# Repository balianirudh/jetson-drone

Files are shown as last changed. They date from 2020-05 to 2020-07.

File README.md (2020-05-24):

# Jetson Drone

I have built two drones with the help of the Cooperative Distributions Systems Lab at the University of Cincinnati. I started working there in the fall of 2018 and have focused on learning different control systems applicable to drones. The first drone I worked on was very rudimentary. It used an Arduino Uno as the main processor and an IMU sensor to monitor the orientation of the drone.

Upon diving deeper into computer vision and more complex control systems, I decided to make a second drone, the Jetson Drone, that is better suited for high-level autonomy. The major improvement compared to the first drone is the integration of the NVIDIA Jetson TX2 and the use of a camera to give the drone hardware that is better suited for autonomy.

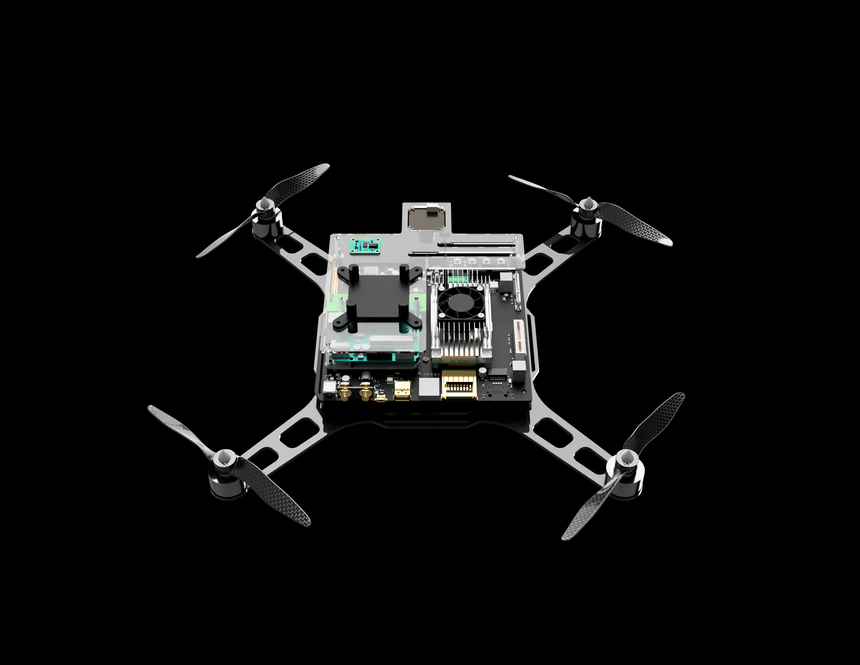
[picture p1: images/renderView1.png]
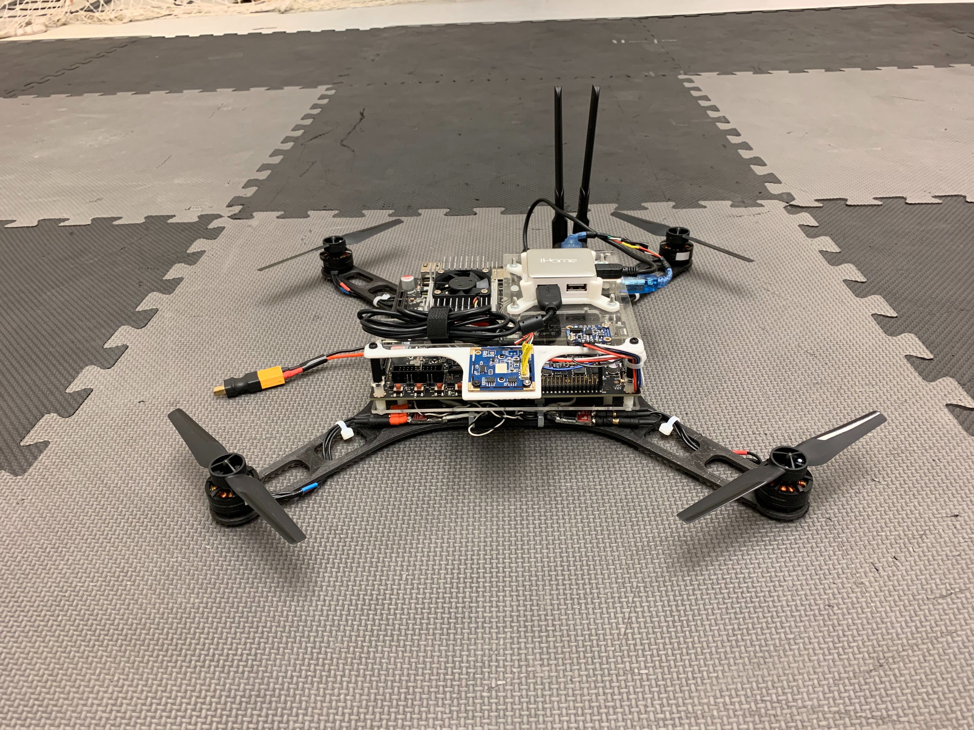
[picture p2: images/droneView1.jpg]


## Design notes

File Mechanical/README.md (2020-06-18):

# Mechancial System

## Frame

The first drone I designed featured laser cut acrylic arms and a top plate that were connected to the power distribtution board by 3D printed brackets. Although this was a sturdy frame and naturally stable due to its weight, it was too heavy for the motor and propeller system I was using. This gave the drone a very short flight time.

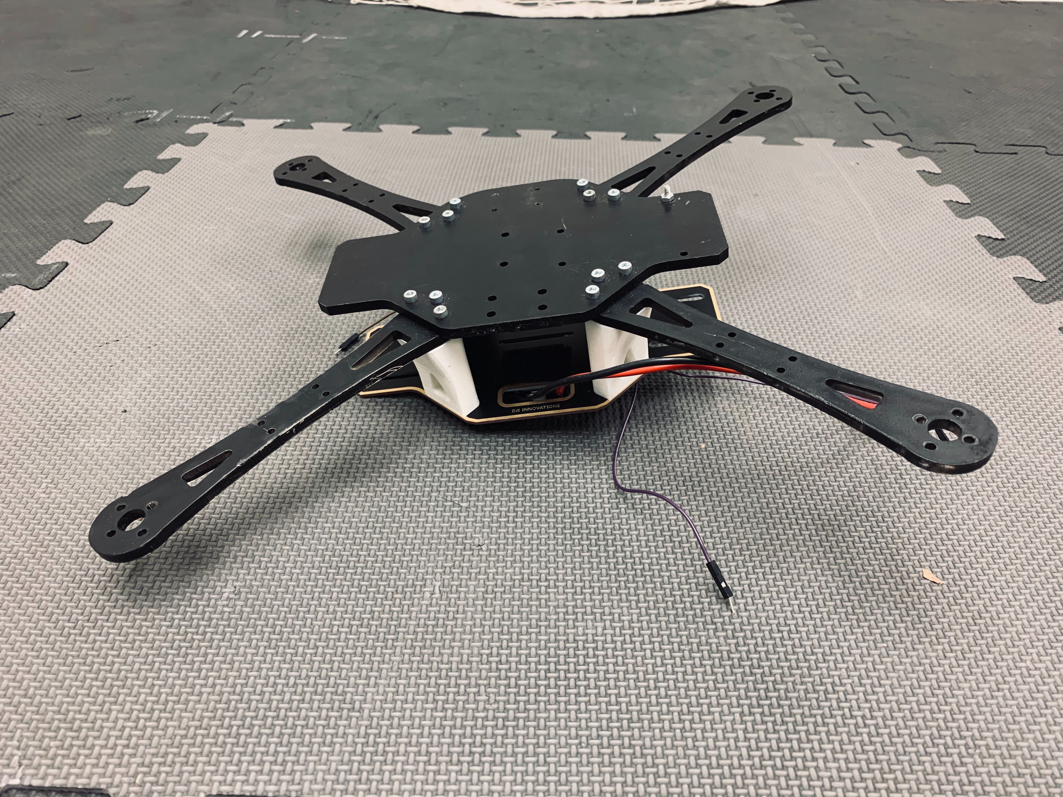
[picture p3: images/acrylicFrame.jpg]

<p align="center">Acrylic frame that was too heavy for prolonged flight times</p>

For the Jetson Drone, I kept in mind speed, agility, and ease of use when designing the frame. Alogn with this, I designed the frame specifically to house the NVIDIA Jetson TX2 carrier board as it has a fairly large footprint compared to most flight controllers used in drones.

The keep the weight low, I decided to 3D print the entire frame. I initially planned to use thinner laser cut acrylic parts but after testing, the thin arcylic arms were too flexible. The frame is made out of two pieces that are held together by a bracket on each side and the electronics mounting structure. However, standard PLA plastic was too flexible even with a high infill. To increase rigidity, I printed the frame out of a chopped carbon fiber and PLA blend. This provides the rigidity necessary in the drone arms while keeping the overall weight of the frame relatively low. 

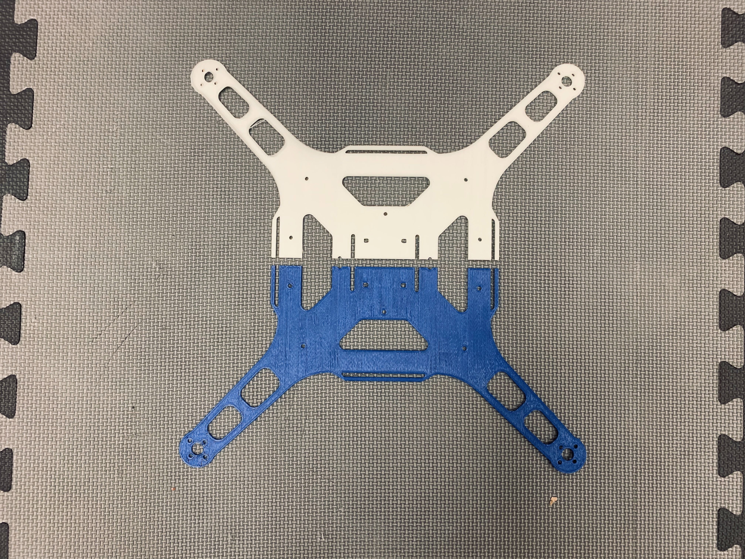
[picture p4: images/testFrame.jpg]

<p align="center">Test 3D print of frame using standard PLA (left), final drone assembly with chopped carbon fiber PLA frame (right)</p>

## Propulsion

The propulsion system of a drone is made up of its motor, electronic speed controller (ESC), and propeller. The combination of the three dictate the total thrust of the drone which impacts the drones overall agility. For the Jetson Drone, I chose to use the DJI Snail Propulstion system. This propulsion system was designed for racing drones meaning its lightweight, and depending on the propeller, has a high max thrust (2800g-5200g).

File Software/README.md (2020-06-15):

# Software

The Jetson TX2 onboard the drone runs Ubuntu 16.04 LTS as the operating system. This gives a tremendous amount of flexibility in regard to how programs can be run on the machine. To fly, the drone is running several different programs that communicate with each other using a publisher-subscriber model. This is done through the robot operating system (ROS) framework to make it a seamless process.

"flowchart of publisher-subscriber model here. refer to portfolio"

## Mobility Control

There are two main controllers that have been implemented on the Jetson drone. The first is a nested PID controller for attitude control. Raw IMU data is processed through a Kalman filter to reduce noise from the IMU. This data is then used by the PID controller to stabilize the drone for any desired orientation.

Rather than using a PID controller for the line following aspect of the drone, I decided to implement an LQR controller. The LQR controller is responisble for calculating each motor's angular velocity to follow a given path. This controller was used because of how it is based on the state-space representation of the system. Unlike other controller, LQR taes into account the dynamics of the drone which is advantageous when trying to move in a specific way.

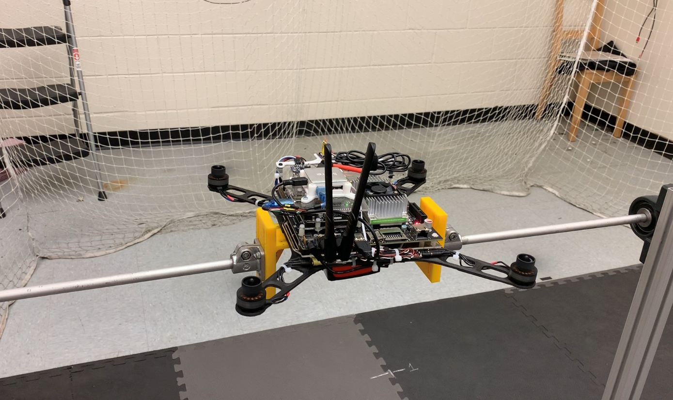
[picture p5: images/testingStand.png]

<p align="center"> Drone on test stand for stability tuning </p>

## Vision System

There are two cameras onboard the Jetson drone; however, currently, only one is being used. The camera that is being used is the downward-facing USB camera. This camera is responsible for taking a live recording of what is below the drone. The video is then  analyzed using OpenCV to determine where the desired path is.

"add flowchart of lane detection"  "add picture of lane detection in action"

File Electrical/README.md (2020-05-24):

# Electrical System

## Flight Controller

The drone carries an NVIDIA Jetson TX2 onboard. This is used as the main flight controller of the drone. The Jetson is capable of doing the necessary computation for video processing and the control system of the drone. Its high computing power made it perfect for the task of creating an autonomous drone and implementing an LQR controller.

Alongside the Jetson, an Arduino Uno is responsible for communicating the motor PWM signals to each ESC. After going through several calculations, the Jetson sends the respective PWM signal of each motor to the Arduino to set the speed of each motor.

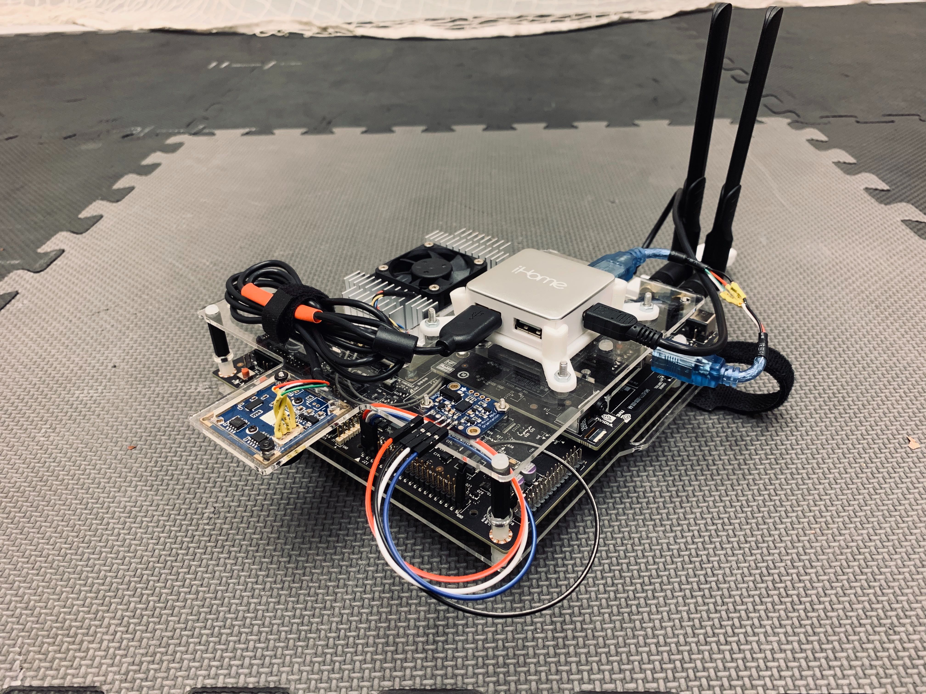
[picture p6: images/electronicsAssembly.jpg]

<p align="center"> Electronics Assembly </p>

## Sensors

There are 3 main sensors on the drone that give it the ability to do what it can do. A BNO055 IMU is connected to the Jeston's GPIO pins. This is necessary to read the current pitch, roll, and yaw angles to make adjustments to maintain a specific orientation. Along with this, 2 cameras are onboard. The main camera is a downward facing USB camera. This camera is meant to identify the path of the desired trajectory for the drone. Using the identified path and the current trajectory of the drone, I am able to calculate the error angle. This angle is used by the LQR controller to calculate the new angular velocities of each motor. 

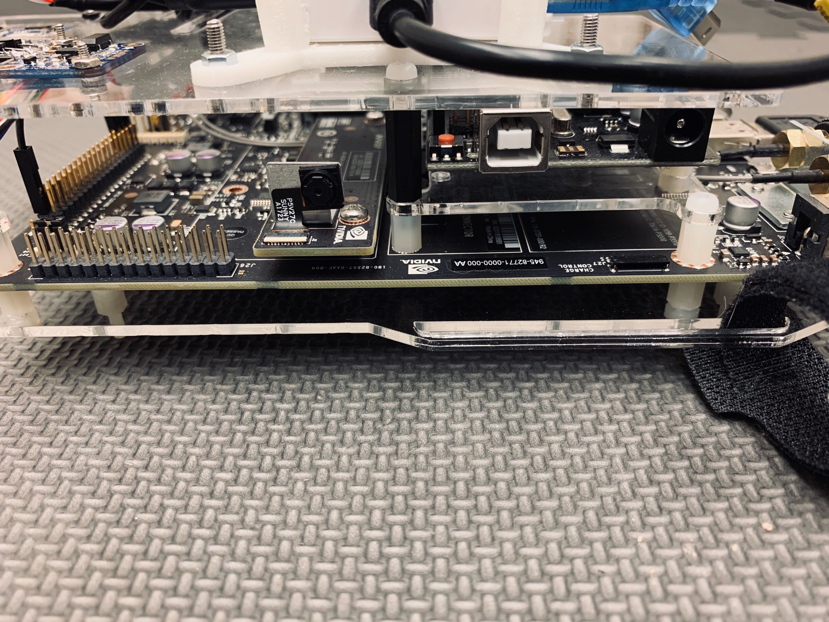
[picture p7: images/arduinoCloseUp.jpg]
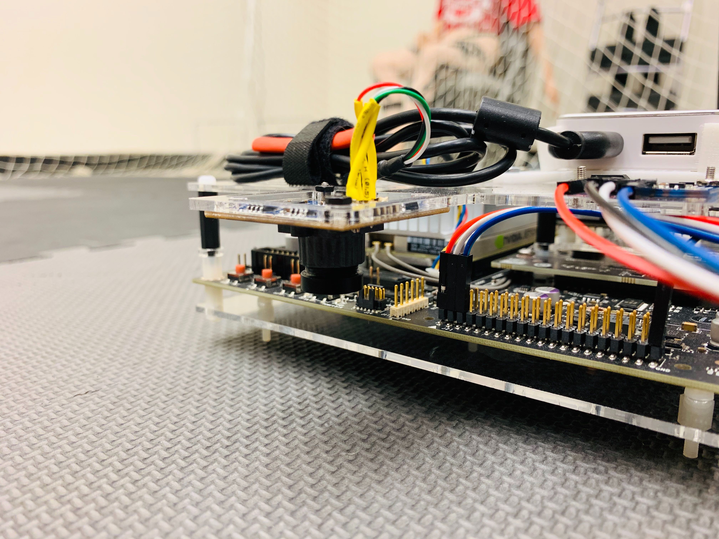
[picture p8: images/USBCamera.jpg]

<p align="center"> Jetson's onboard camera and mounted Arduino (left), Downward facing USB camera for line following (right) </p>

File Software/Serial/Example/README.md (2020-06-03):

# Serial Communication with Arduino LED

*Current code only works on Windows. In Linux, the data is sending to the Arduino and the Arduino is receiving it but I don't see the correct behavior from the LED. I believe the problem is that I need to configure the path of the Arduino so the Arduino recieved the correct data. Looking into how I can solve this issue.*

Serial communication is vital to the function of the drone because without it the drone would not receive motor commands. I am sure there is a way to use the GPIO pins of the Jetson to send PWM signals to the motor controllers, however, the Arduino platform makes this task straightforward. 

The purpose of this example to is demonstrate how the serial communication between the Jetson TX2 and Arduino Uno work on the drone. With this example, there is no need to calculate specific motor values or have the full ROS package of this project set up. Instead it uses the Arduino's onboard LED to demonstrate how data is being sent from a C++ program to the Arduino.

Note that even though the C++ program only sends data to the Arduino once, the Arduino's onboard LED continously blinks using data that was only sent once. This is because the variable receivedInts (in Arduino program) is never written over with new data and the function that blinks the LED is in a loop.

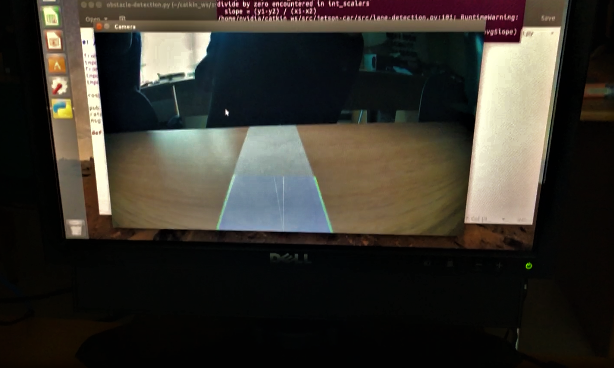
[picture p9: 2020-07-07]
images/pathDetectionExample.png

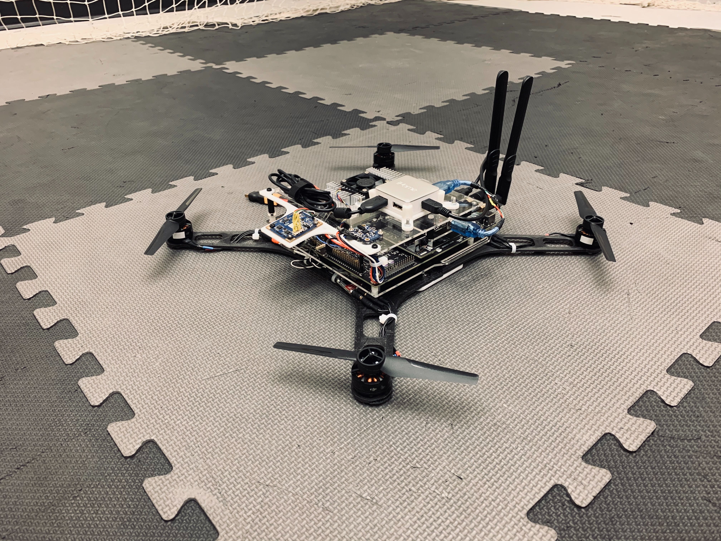
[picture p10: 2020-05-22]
images/droneView3.jpg

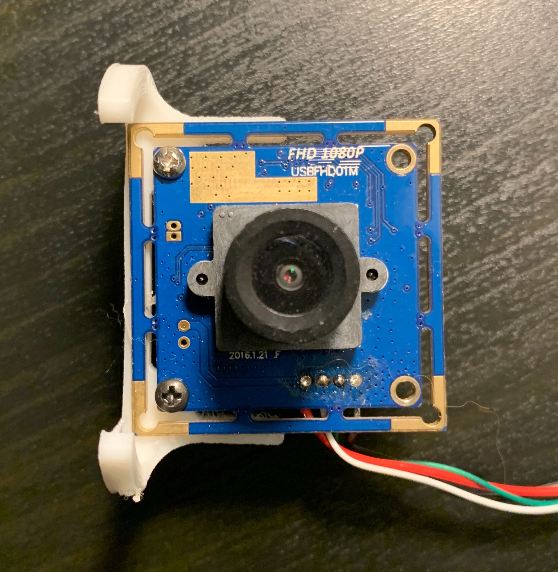
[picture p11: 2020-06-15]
images/USBCamera2.jpg

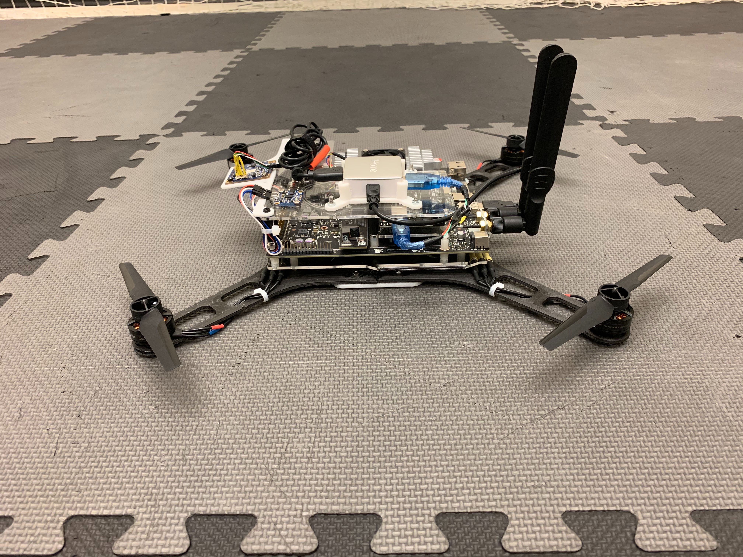
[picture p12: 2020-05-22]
images/droneView2.jpg

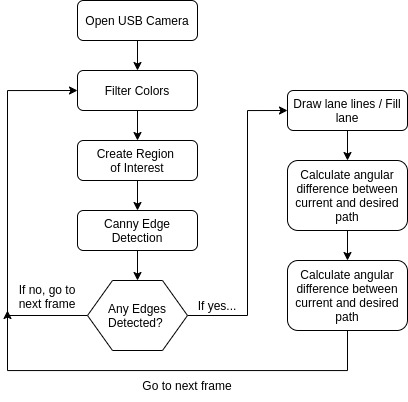
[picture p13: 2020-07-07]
images/videoProcessing1.jpg

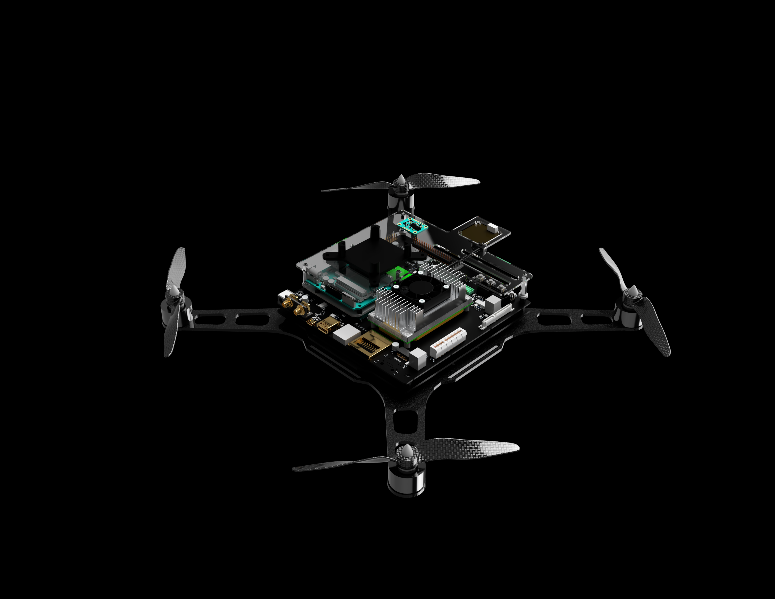
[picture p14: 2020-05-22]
images/renderView3.png

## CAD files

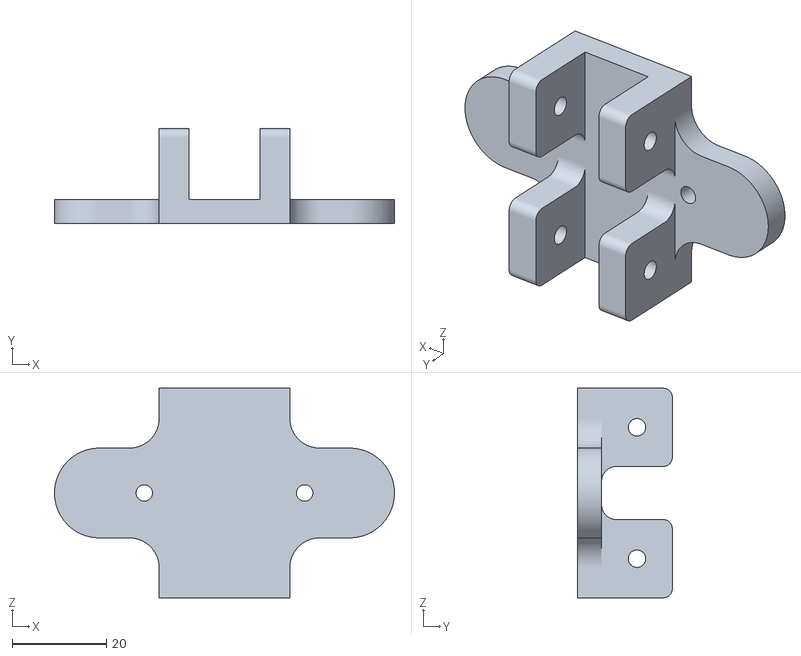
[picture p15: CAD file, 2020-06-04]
Mechanical/CAD/3DPrint/TestBracket.stl
72.1 x 20.1 x 44.4

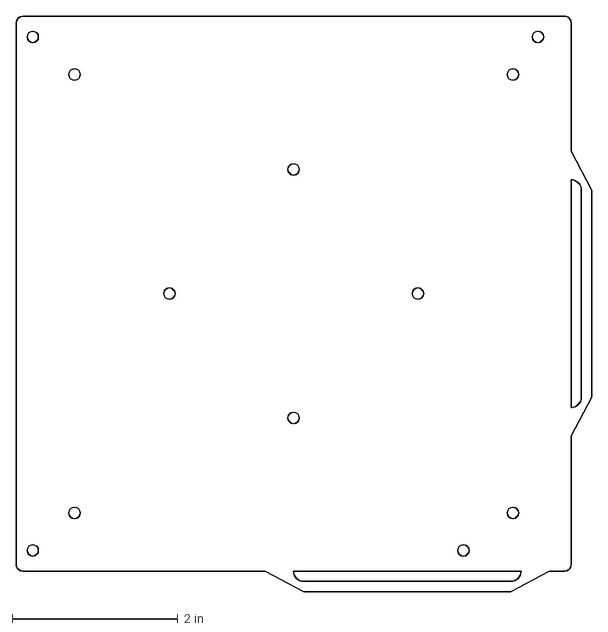
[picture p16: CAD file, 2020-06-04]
Mechanical/CAD/Lasercut/secondLayer.dxf
6.95 x 6.95 in

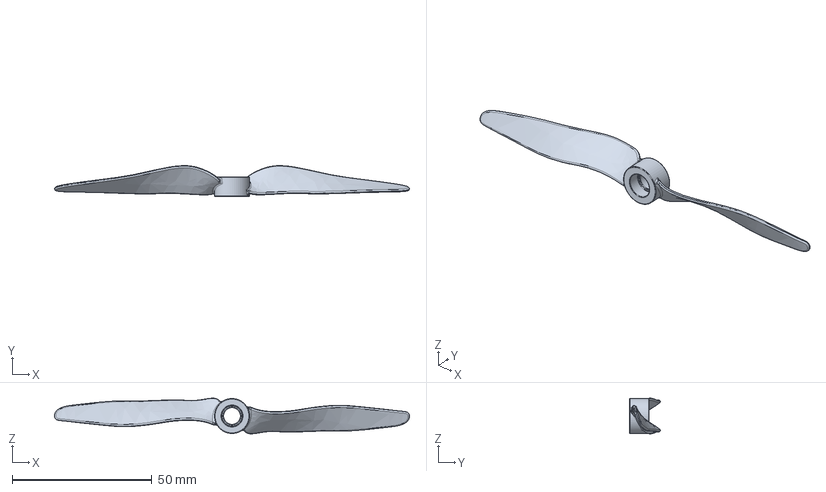
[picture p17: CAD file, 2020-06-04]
Mechanical/CAD/Propeller 5x5.step
127.0 x 11.0 x 12.8 mm

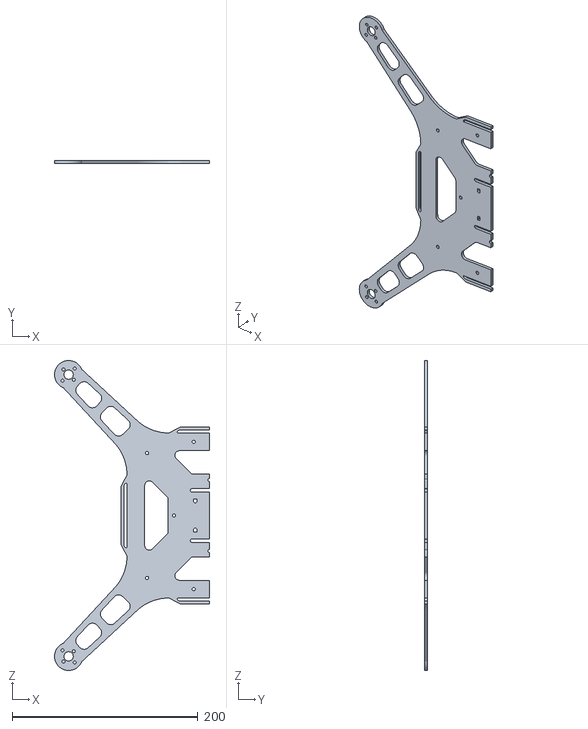
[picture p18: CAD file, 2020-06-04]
Mechanical/CAD/3DPrint/HalfFirstLayer.stl
167.0 x 3.17 x 334.0

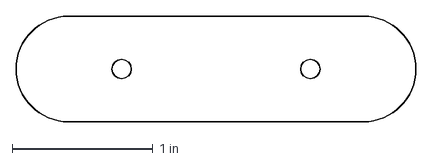
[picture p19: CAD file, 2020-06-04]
Mechanical/CAD/Lasercut/FrameBracket.dxf
2.84 x 0.75 in

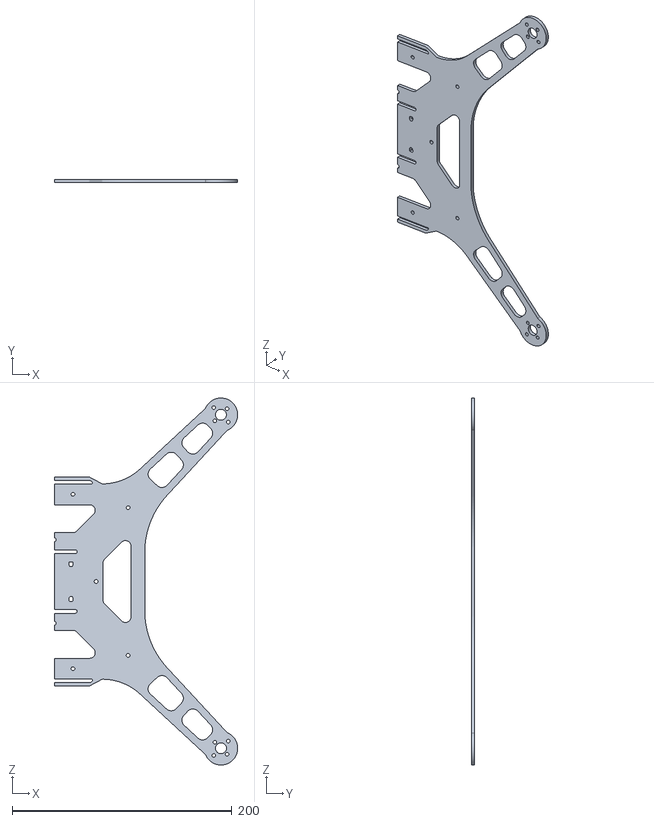
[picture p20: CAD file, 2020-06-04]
Mechanical/CAD/3DPrint/SecondHalf.stl
167.0 x 3.17 x 334.1

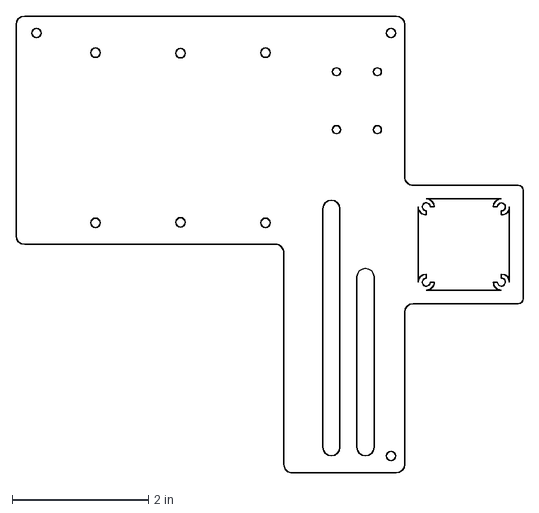
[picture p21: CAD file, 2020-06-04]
Mechanical/CAD/Lasercut/thirdLayer.dxf
7.43 x 6.70 in

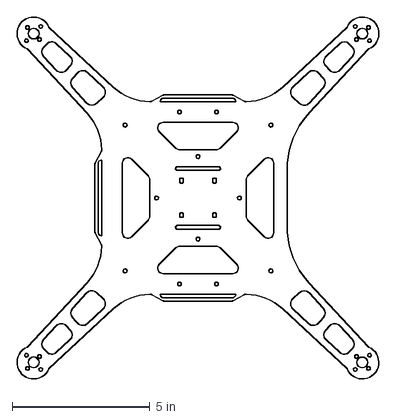
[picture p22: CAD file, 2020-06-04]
Mechanical/CAD/Lasercut/firstLayer.dxf
13.2 x 13.2 in

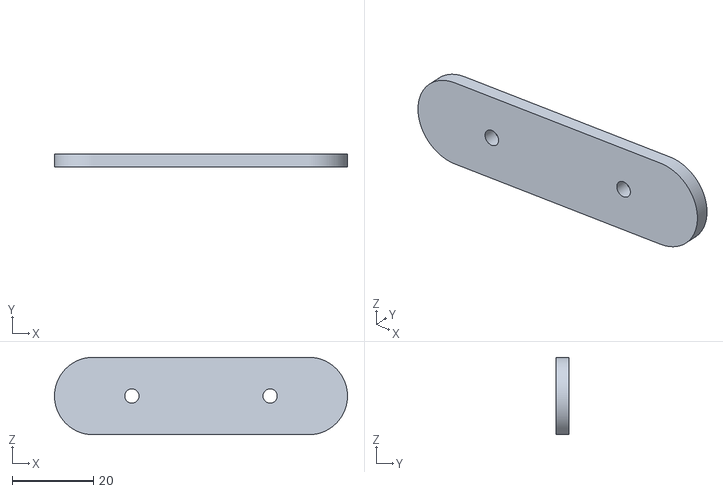
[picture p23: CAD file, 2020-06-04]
Mechanical/CAD/3DPrint/FrameBracket.stl
72.1 x 3.17 x 19.0

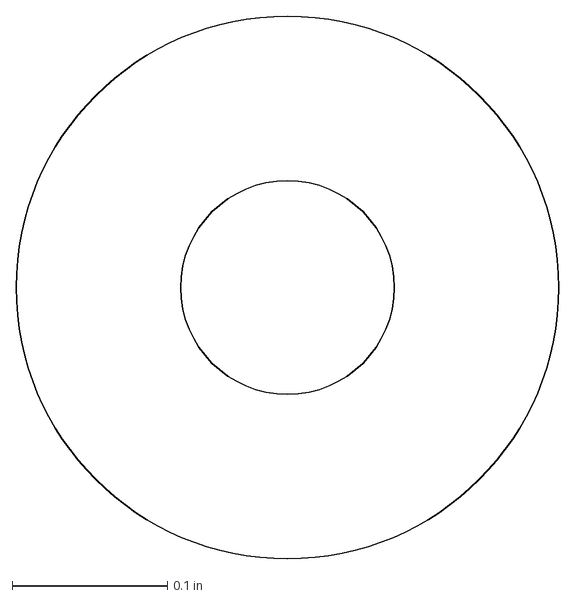
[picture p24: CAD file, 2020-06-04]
Mechanical/CAD/Lasercut/spacer.dxf
0.35 x 0.35 in

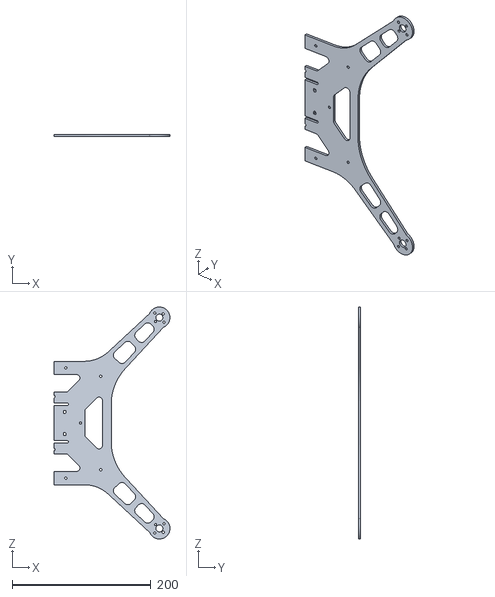
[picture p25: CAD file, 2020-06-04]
Mechanical/CAD/3DPrint/SecondHalf2.stl
167.0 x 3.17 x 334.1

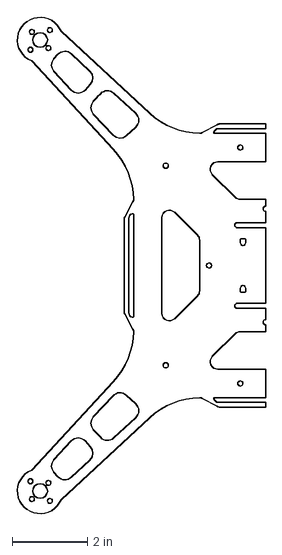
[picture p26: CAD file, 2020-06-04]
Mechanical/CAD/Lasercut/halfFirstLayer.dxf
6.60 x 13.2 in

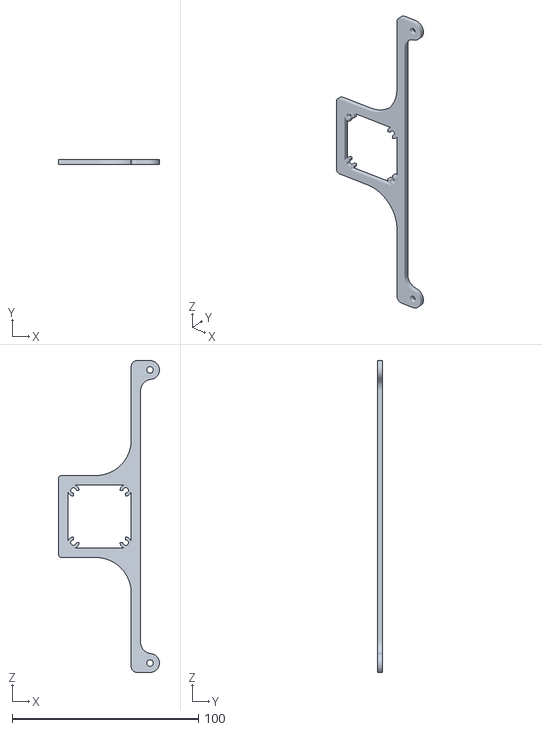
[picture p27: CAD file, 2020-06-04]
Mechanical/CAD/3DPrint/CameraBracket.stl
54.2 x 2.54 x 167.6

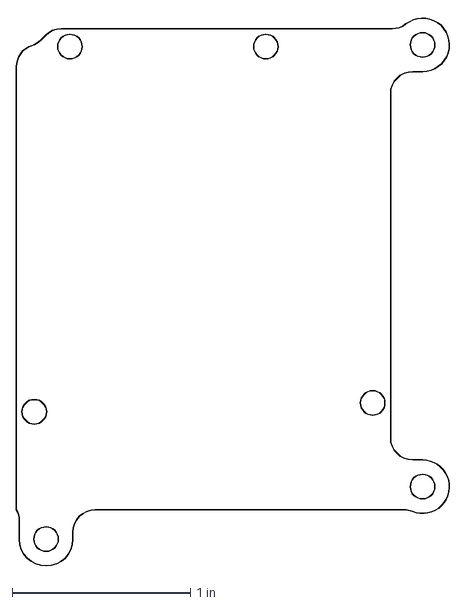
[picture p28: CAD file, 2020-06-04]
Mechanical/CAD/Lasercut/arduinoPlate.dxf
2.44 x 3.09 in

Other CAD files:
Mechanical/CAD/3DPrint/HalfFirstLayer2.stl
Mechanical/CAD/3DPrint/FirstLayer.stl
archives/FlameWheelFrame/FlameWheel_F450_Base_Bottom.SLDPRT
Mechanical/CAD/7x7 Propeller.ipt
Mechanical/CAD/Adafruit_BNO055_AP214.ipt
Mechanical/CAD/ArduinoPlate.ipt
Mechanical/CAD/CameraBracket.ipt
Mechanical/CAD/CameraMount.ipt
Mechanical/CAD/FirstLayer.ipt
Mechanical/CAD/FrameBracket.ipt
Mechanical/CAD/Hex Spacer MF M3 L20mm.ipt
Mechanical/CAD/Hex Spacer MF M3 L6mm.ipt
Mechanical/CAD/Hex Spacer MF M3 L8mm.ipt
Mechanical/CAD/LOW-LIGHT-HD-USB-CAMERA-R1.ipt
Mechanical/CAD/MotorMountingHub.ipt
Mechanical/CAD/Propeller 5x5.ipt
Mechanical/CAD/SecondLayer.ipt
Mechanical/CAD/SnailMotorModel.ipt
Mechanical/CAD/TestBracket.ipt
Mechanical/CAD/ThirdLayer.ipt
Mechanical/CAD/USBHubMount.ipt
Mechanical/CAD/spacer.ipt
archives/FlameWheelFrame/FlameWheel_F450.iam
archives/FlameWheelFrame/FlameWheel_F450_Base_Bottom.ipt
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

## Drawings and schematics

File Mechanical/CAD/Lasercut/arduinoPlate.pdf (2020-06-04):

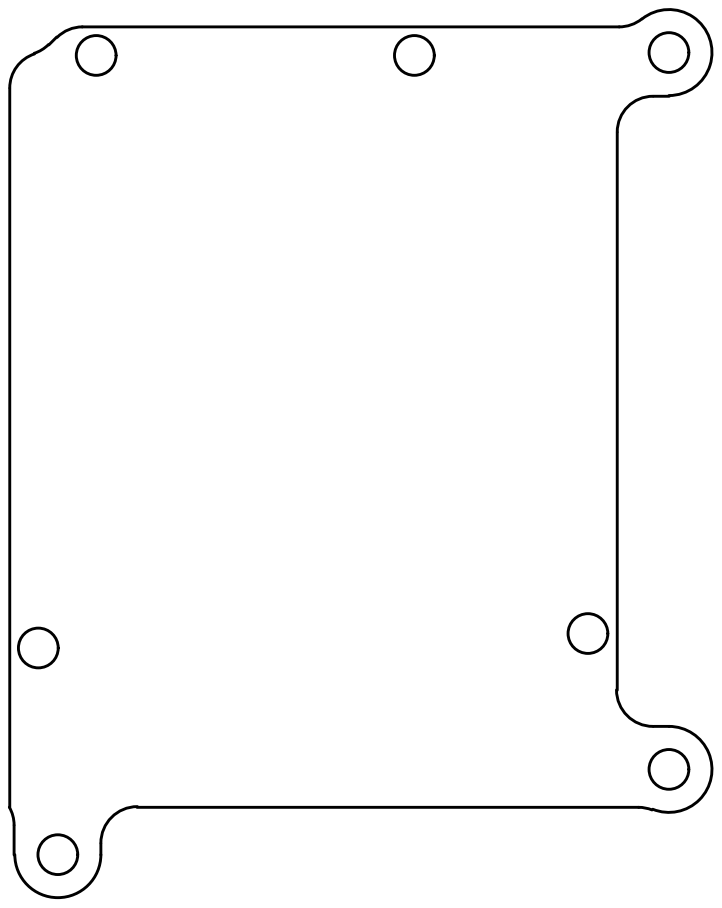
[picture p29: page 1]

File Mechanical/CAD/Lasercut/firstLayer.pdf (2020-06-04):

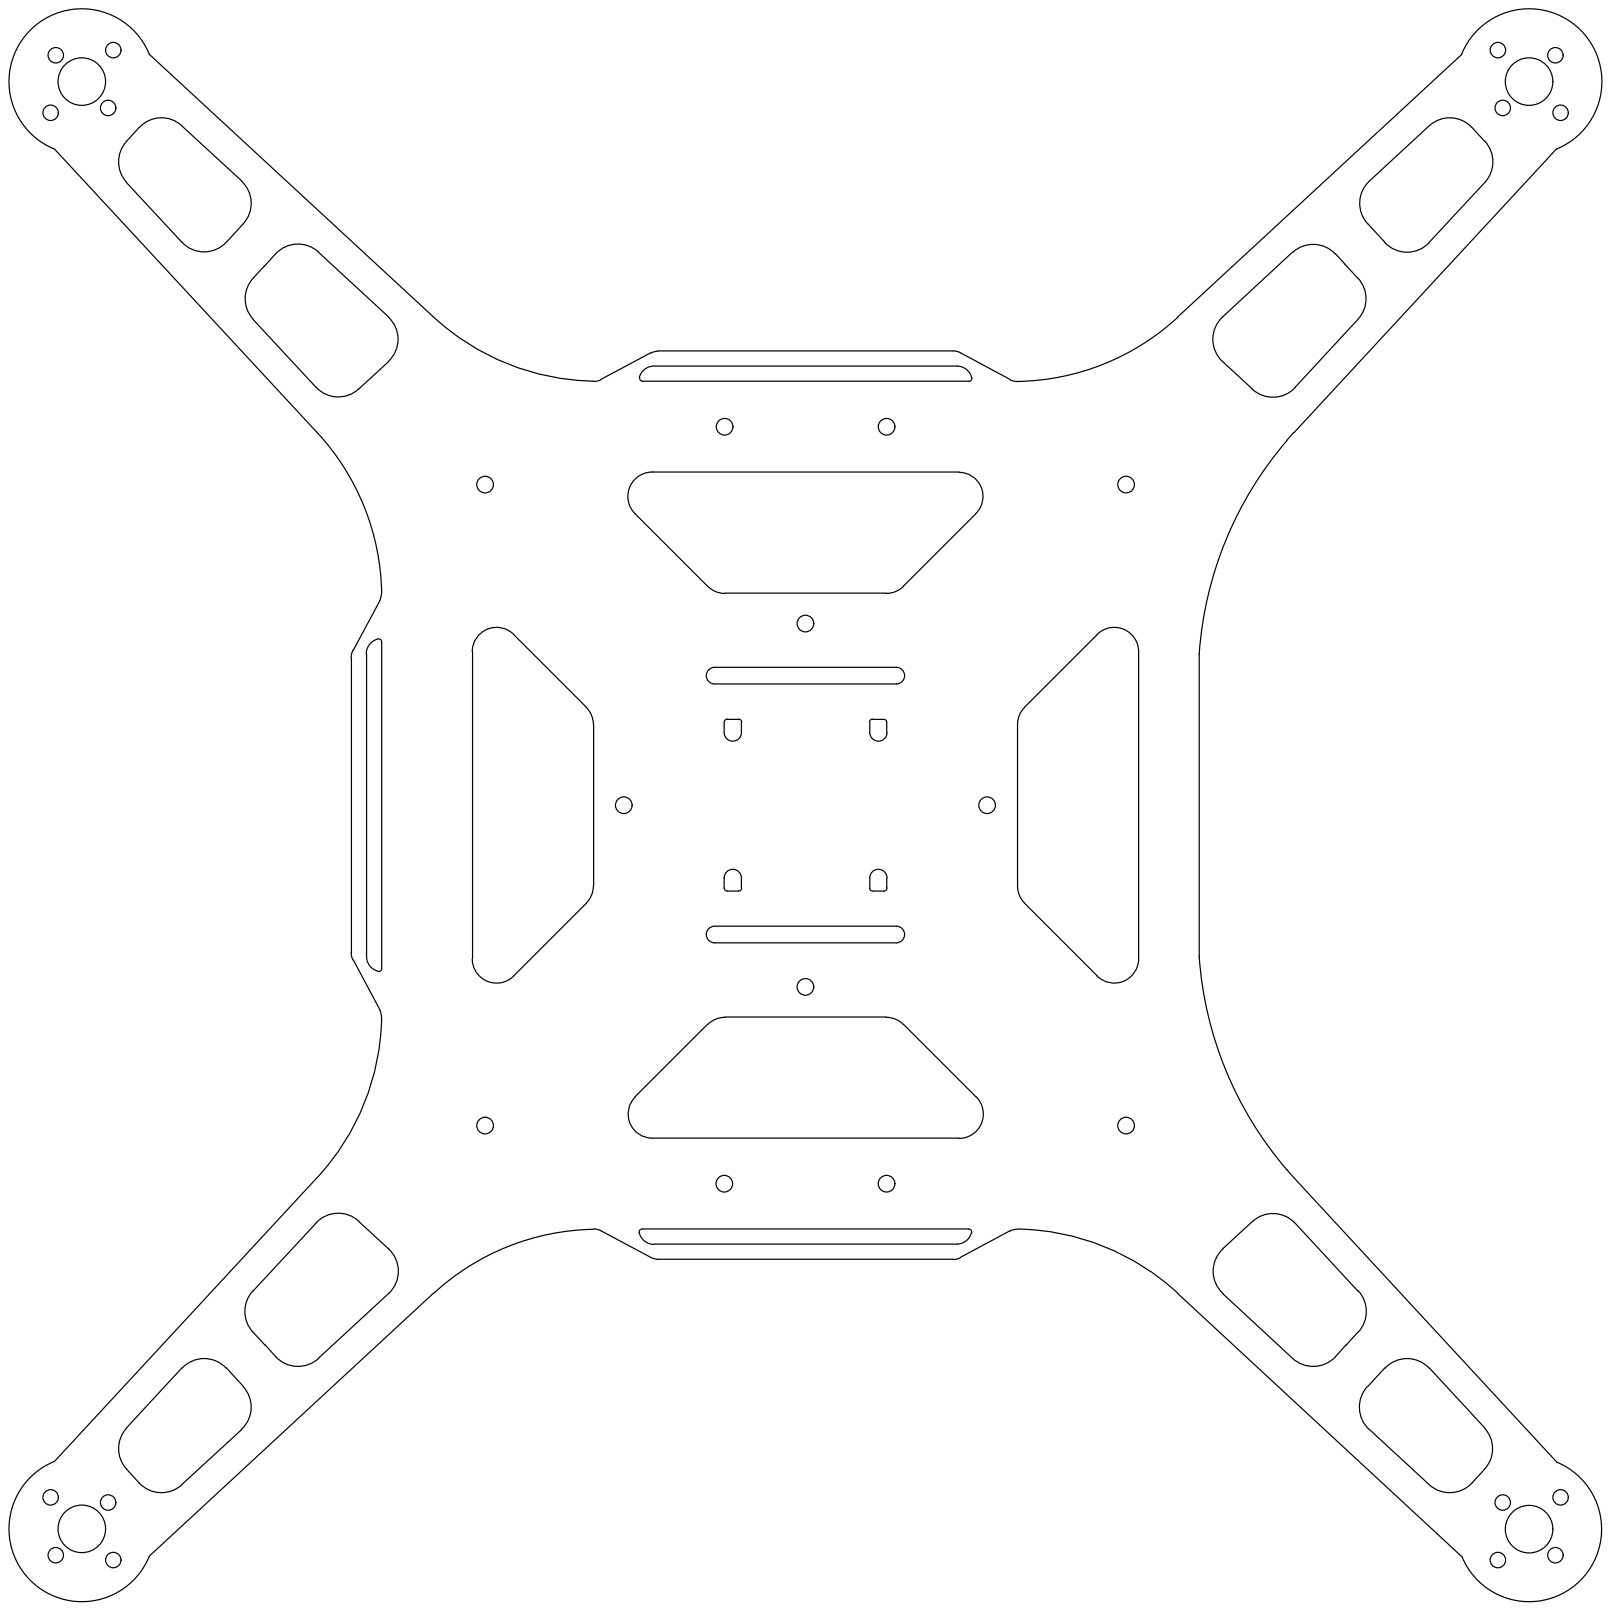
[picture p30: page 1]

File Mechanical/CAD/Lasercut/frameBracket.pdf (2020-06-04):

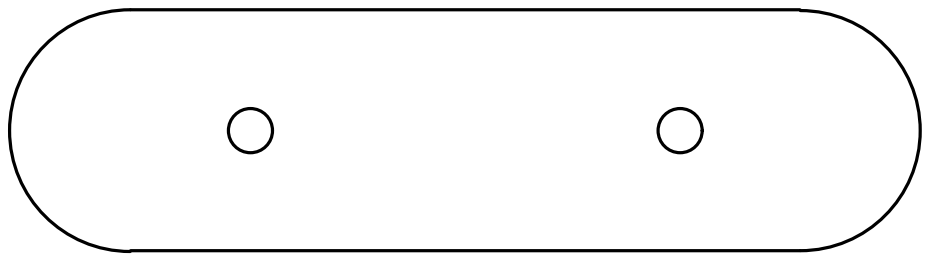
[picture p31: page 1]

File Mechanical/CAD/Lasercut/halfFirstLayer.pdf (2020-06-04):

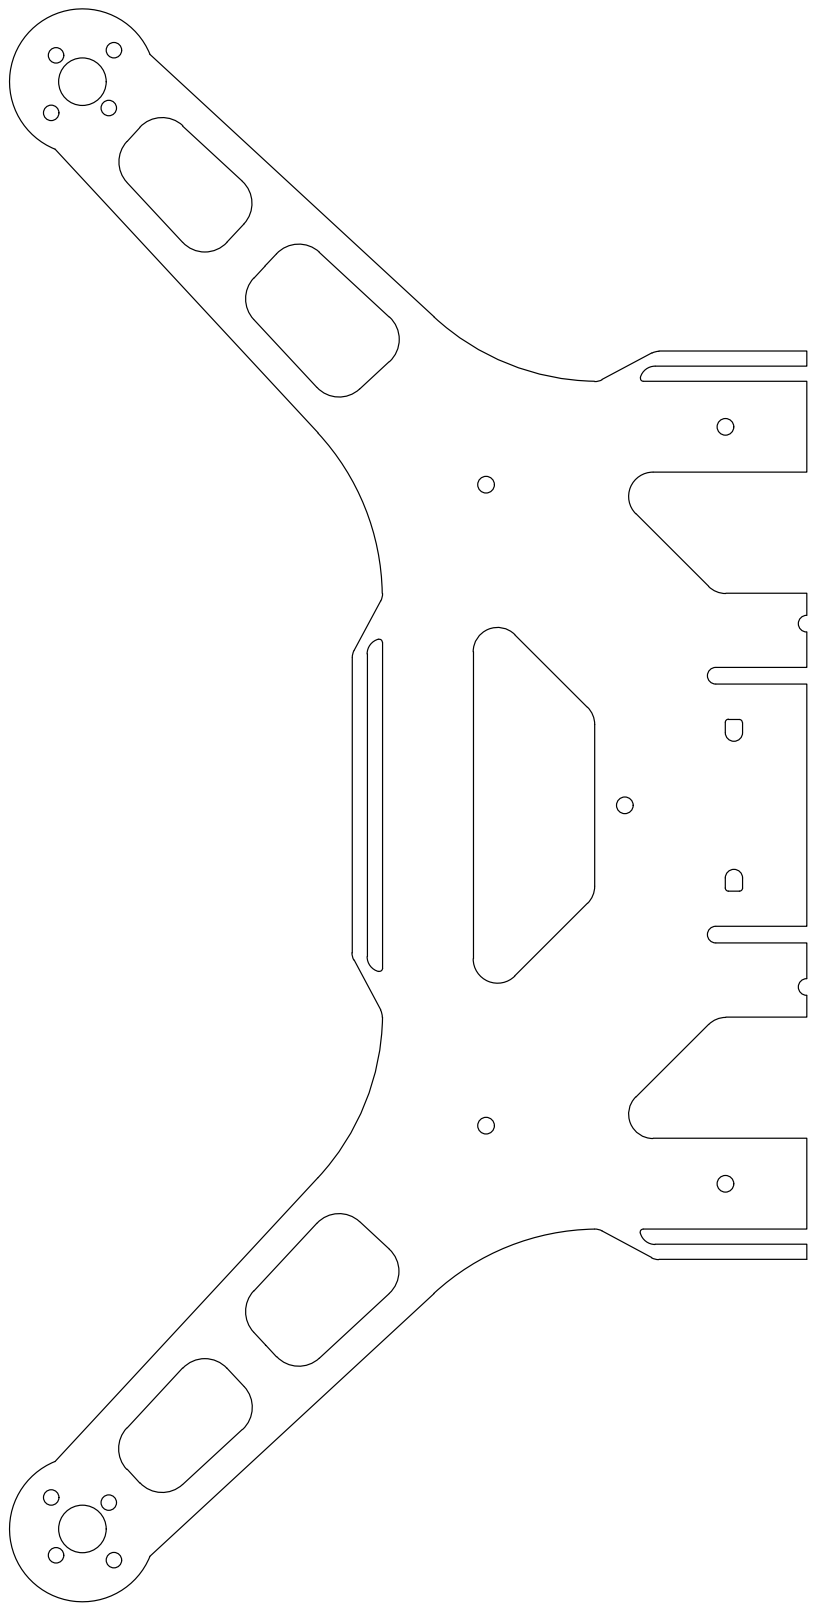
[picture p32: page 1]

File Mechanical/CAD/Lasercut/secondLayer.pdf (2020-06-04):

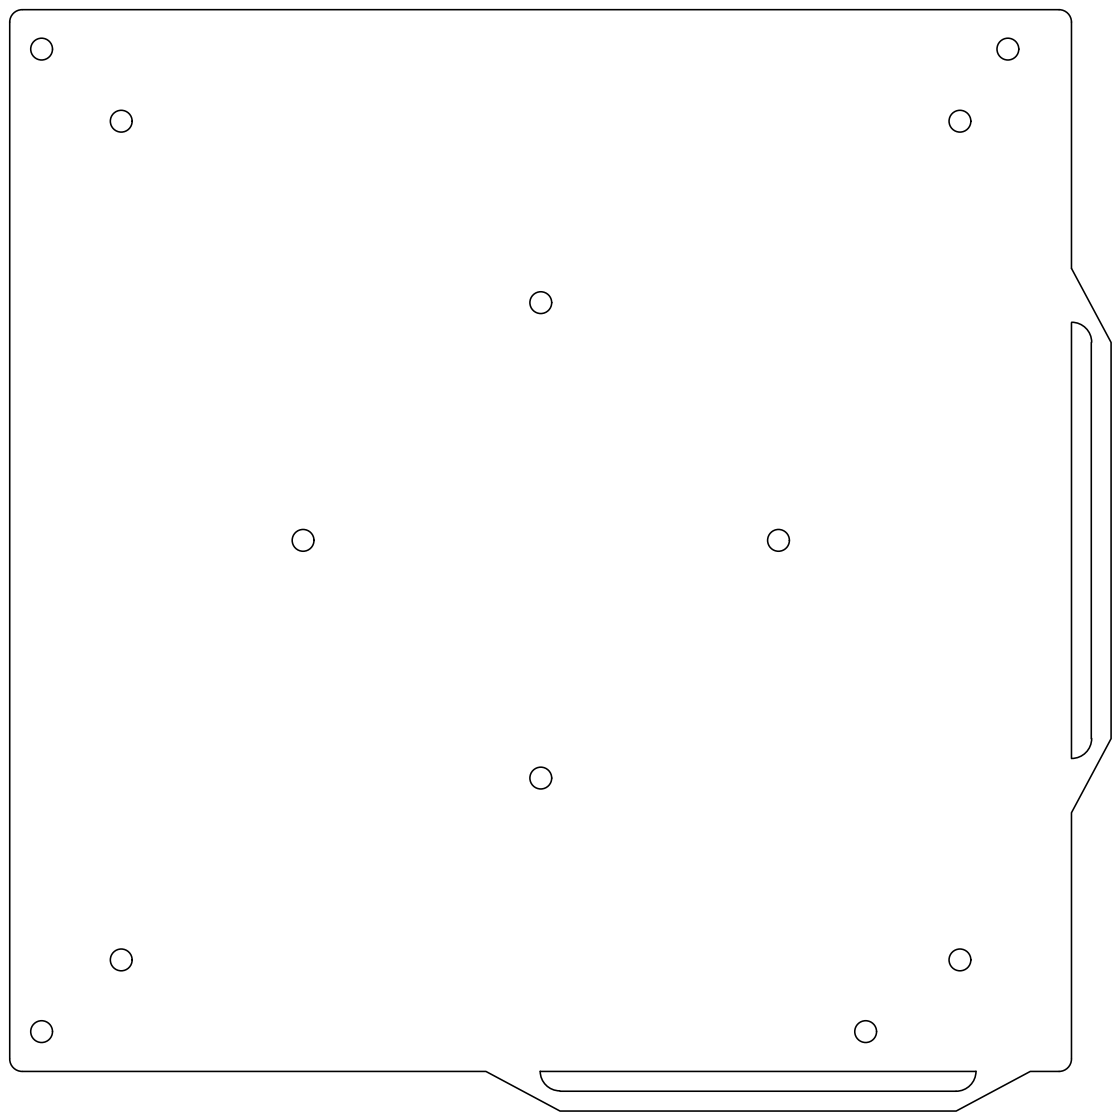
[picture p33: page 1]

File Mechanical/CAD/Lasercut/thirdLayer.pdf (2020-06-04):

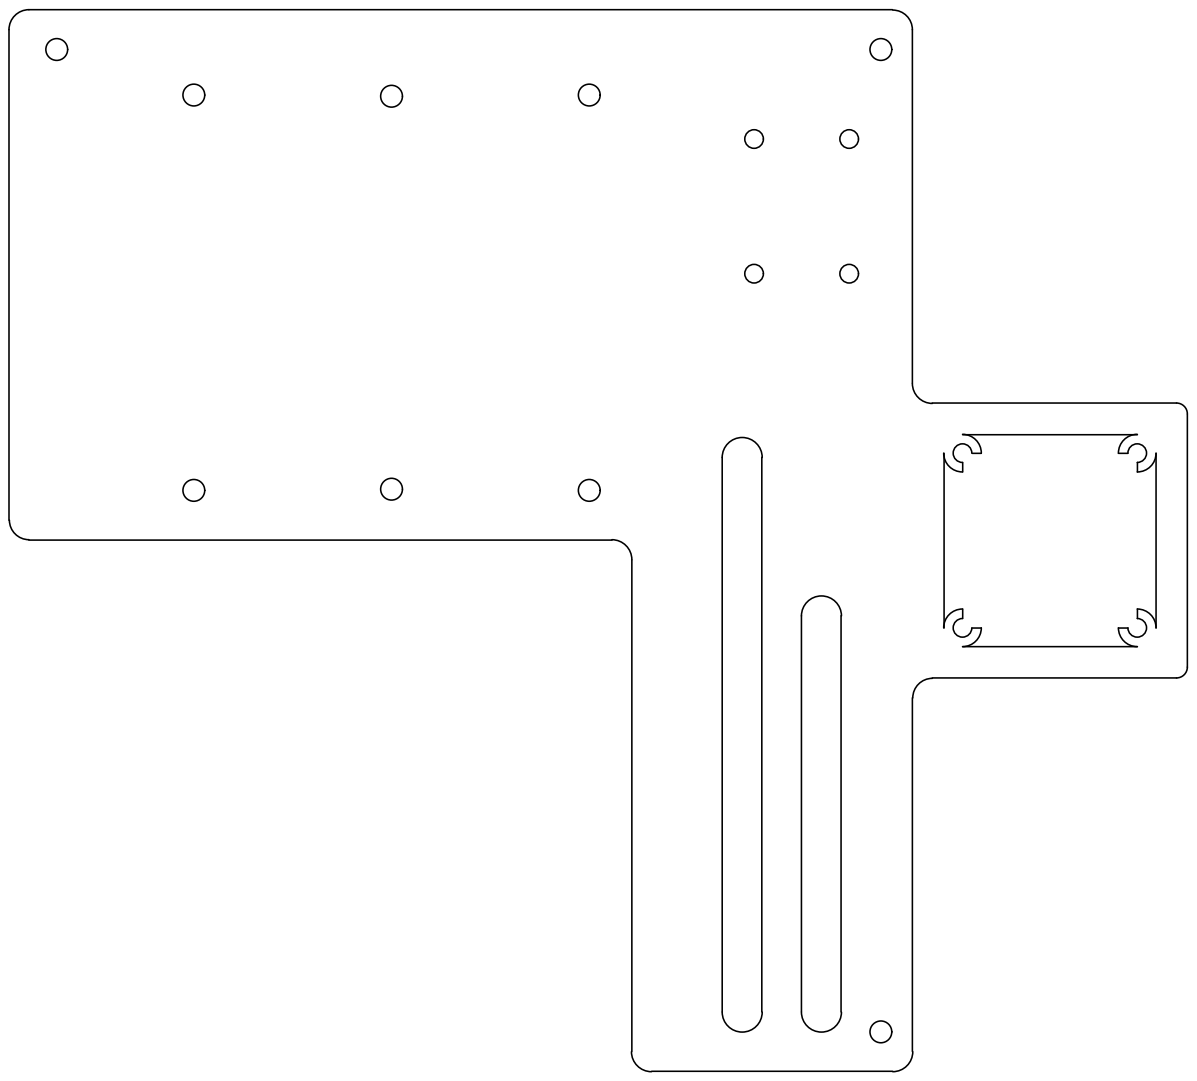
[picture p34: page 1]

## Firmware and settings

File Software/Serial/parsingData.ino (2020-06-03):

/*
Parsing Data

The purpose of this program is to parse data that is sent to the Arduino from the Jetson. This is an important part of the serial communication process between
the Jetson and Arduino because the Jetson sends the four motor PWM signals together as an array of characters in the form "<pwm1|pwm2|pwm3|pwm4>". For the
Arduino to use this data to set motor speeds, it needs to parse the data into the four PWM signals and convert them to integers. This code covers specifically
how the Arduino indentifies the four PWM signals and how they are converted to integers.

For simplicity purposes, the data is just declared in this program rather than having it being sent from a different program. Because of this, the start and
end markers (< and >) are not included in the data character array. If you are interested in how data is actually recieved by the Arduino, please refer to the
serialRead.ino program.

last modified 06/03/2020
by Anirudh Bali
*/

int numData; //stores integer form of parsed sent data

void setup() {
  Serial.begin(115200); //Starting serial for testing purposes
  while(!Serial) {
    ; //waiting for serial port to connect
  }
}

void loop() {
  char data[] = "1234|1567|1789|2000"; //data from jetson, representative of the four motor values being sent to arduino "pwm1|pwm2|pwm3|pwm4"
  char * pch; //pointer to parse the sent data

  pch = strtok (data, "|"); //get first token, function works by reading each char and storing in pch until it reads "|"
  while(pch != NULL) {
    numData = atoi(pch); //converts pch to an integer
    Serial.print(pch); //prints pch
    Serial.print("     ");
    Serial.println(numData); //prints integer form of pch
    pch = strtok (NULL, "|"); //get next token
  }
  delay(5000);
}

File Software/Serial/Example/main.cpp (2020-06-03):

/*
LED Example

This LED Example code is meant to demonstrate the serial communication between the Jetson and Arduino. With this program, there is no need to calculate
different motor values, instead, a C++ file sends data that tells the Arduino how long to turn off its onboard LED. This code is responsible for sending the
data to the Arduino from a C++ program that is used to turn off an LED. What you should see is that the Arduino's onboard LED should turn on for 2 seconds and 
turn off for 3 seconds in a loop.

last modified 05/31/2020
by Anirudh Bali
*/

#include <iostream>
#include <stdio.h>
#include <string.h>

using namespace std;

char serialPortFilename[] = "COM3"; //file path of Arduino, in Windows this is a COM port, in Linux it follows the
                                    // form /dev/ttyACM0 or /dev/ttyUSB0 depending on the distribution

int main()
{
    FILE * serPort = fopen(serialPortFilename, "w"); //defining and opening Arduino COM port, "w" indicates writing to this file

    if(serPort == NULL)
    {
        printf("ERROR"); //check if Arduino file path exists, if it doesn't send ERROR message
        return 0;
    }

    char writeBuffer[] = {"<3000>"}; //data that is being sent to Arduino, need start and end markers (<, >)
                                     //this data is used as a delay for how long the Arduino onboard LED stays off
                                     //delay is in milliseconds
    fwrite(writeBuffer, sizeof(char), sizeof(writeBuffer), serPort); //sending data to Arduino
    //first parameter is array of elements, second is size of each element, third is number of elements,
    //fourth is Arduino file path

    fclose(serPort); //close Arduino file path once data is sent
    return 0;
}

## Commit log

2020-05-19 Updated documentation on frame
2020-05-19 Documented flight controller and sensors
2020-05-22 Uploaded current images of drone
2020-05-24 Updated flight controller and sensors
2020-06-04 Uploaded all CAD files
